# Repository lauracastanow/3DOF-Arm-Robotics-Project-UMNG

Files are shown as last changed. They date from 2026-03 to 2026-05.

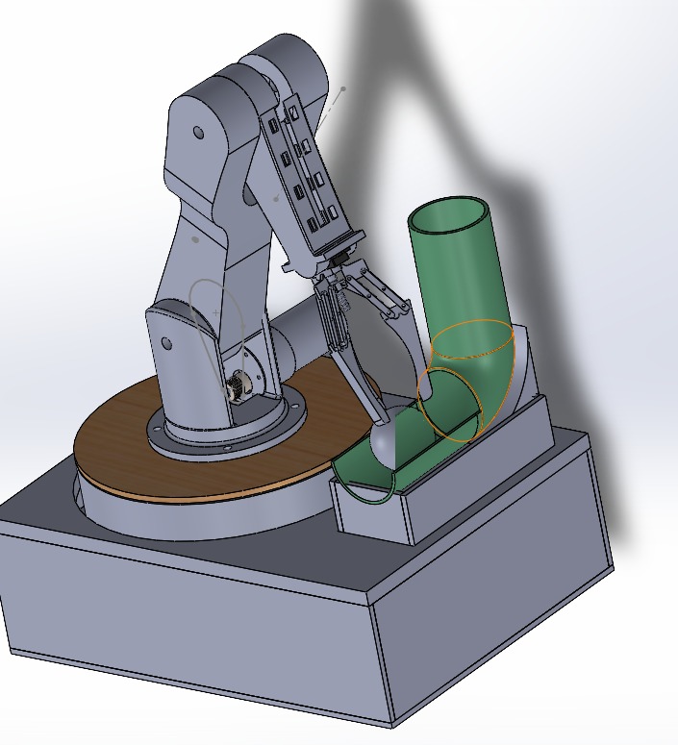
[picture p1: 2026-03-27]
Docs/Ensamblaje General SW.jpeg

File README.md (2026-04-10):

# 3DOF-Arm-Robotics-Project-UMNG
Este proyecto consiste en el diseño, modelado y simulación de un brazo robótico de 3 grados de libertad. En el siguiente repositorio, se incluye el desarrollo mecánico en CAD, simulación en software, código de control y una interfaz interactiva para visualizar la cinemática inversa. 

## Objetivos
### Objetivo General
Diseñar un brazo robótico integrando herramientas de hardware (CAD) y software (ROS 2, Gazebo, Python) para la posición del efector final mediante el cálculo de la cinemática y control de los actuadores en tiempo real.

### Objetivos Específicos
* Diseñar la estructura mecánica del brazo y su exportación a formato URDF.
* Modelar matemáticamente el sistema para implementar cinemática directa e inversa.
* Configurar con la simulación física en Gazebo Sim (Dynamics, colisiones e inercias).
* Establecer comunicación en tiempo real entre ROS 2 y Gazebo usando 'ros_gz_bridge'.
* Desarrollar una interfaz gráfica de usuario (GUI) interactiva para el control articular.

---

## Estructura del repositorio
El proyecto está modularizado basándose en el diagrama de bloques del sistema:

* 'Docs/' Diagramas de bloques, actas de trabajo y capturas de funcionamiento.
* 'Hardware/' Diseño CAD, mallas (meshes) y el archivo de descripción 'Ensamblee.urdf'.
* 'Simulación/' Archivos de lanzamiento ('gazebo.launch.py') y configuración del entorno virtual.
* 'Software/' Lógica de control, cinemática ('kinematics.py'), y nodo de ROS 2 conectado a la GUI ('gui.py')

---

## Descripción del sistema
El robot ("Bracito") es un manipulador que cuenta con los siguientes grados de libertad controlables:

* **Joint 1 (Base):** Rotación sobre el eje Z.
* **Joint 2 (Hombro):** Elevación del primer eslabón.
* **Joint 3 (Codo):** Elevación del segundo eslabón.
* **Joints 4, 5 y 6:** Pinza de 3 dedos configurada con plugins *Mimic* en Gazebo, permitiendo que la actuación de un solo motor cierre o abra la pinza completa de manera síncrona.

Ensamblaje General SolidWorks

El modelo permite calcular:
* Cinemática inversa
* Posición del efector final
Interfaz de Control Maestro y Gazebo funcionando

---

## Paquetes, Dependencias y Librerías
Para la correcta ejecución de etse proyecto, es necesario contal con el siguiente entorno:

**Entorno Base:**
* Ubuntu 24.04 (o compatible)
* [ROS 2 Jazzy] (https://docs.ros.org/en/jazzy/index.html)
*  Gazebo Sim (Harmonic)

**Librerías de Python:**
* 'rclpy' (Cliente de ROS 2 para Python)
* 'PyQt5' (Desarrollo e la interfaz gráfica)
* 'numpy' (Cálculos matriciales para la cinemática)

**Paquetes de ROS 2 utilizados:**
* 'robot_state_publisher': Para publicar el estado del robot basado en el URDF.
* 'ros_gz_sim': Para instanciar (spawn) el modelo en Gazebo.
* 'ros_gz_bridge': Para traducir los tópicos de 'JointState' / 'Float64' entre ROS 2 y Gazebo.

---

## Autoras
Proyecto desarrollado por estudiantes de Ingeniería de la Universidad Militar Nueva Granada (UMNG):
* **Laura Daniela Castaño Silva**
* **Carol Tatiana Jeréz González**

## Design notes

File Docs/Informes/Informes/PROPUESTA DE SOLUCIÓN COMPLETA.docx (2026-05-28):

## PROPUESTA DE SOLUCIÓN COMPLETA

Castaño Silva Laura Daniela, Carol Tatiana Jérez González, Hugo Alejandro Chacon Valderrama

{est.laura.castano, est.carol.jerez, hugo.chacon}@unimilitar.edu.co

Profesor: Alexandra Elizabeth Velasco Vivas

I. PROCEDIMIENTO

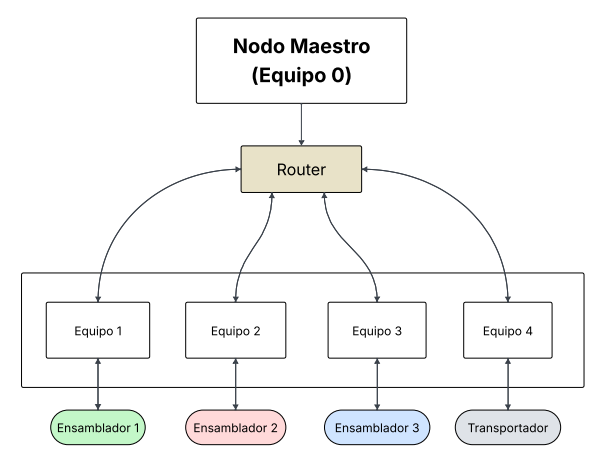
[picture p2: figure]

Figura 1. Diagrama de Bloques - Parte General.

En este caso, se va a mantener el mismo ideal de tener 5 equipos en funcionamiento, donde los equipos del 1 al 4 van a estar a cargo de los ensambladores y el transportador, sin embargo, el equipo 0 se va a usar para la comunicación general de todos los equipos, en este caso, se busca hacerlo por medio de un Router.

En este caso, seríamos el ensamblador tres.

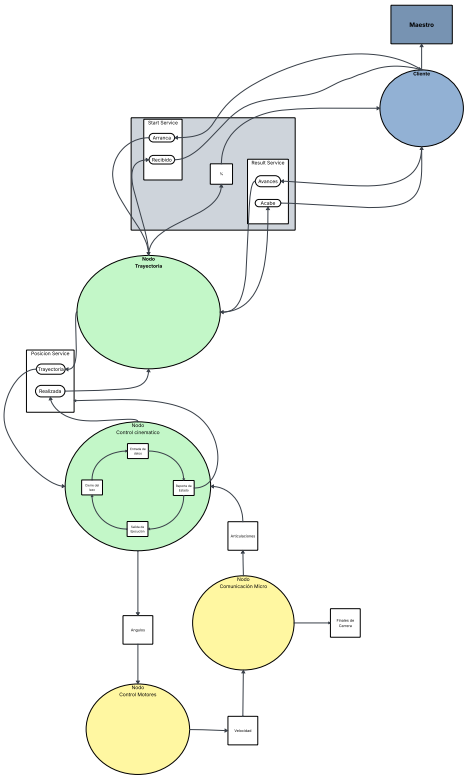
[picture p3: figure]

Figura 2. Diagrama de Bloques con cada nodo.

Para la implementación de la etapa de control se plantea un funcionamiento basado en el entorno de trabajo dispuesto por “Robot Operating System 2” - “ROS ²” el cual permite la comunicación coordinada entre los sistemas internos de un robot así como entre sistemas independientes (otros robots) por medio del intercambio de datos entre “nodos” dedicados por sistema (Control, Sensores, Actuadores, Cinemática Directa\Inversa, Robot 1, Robot 2,..etc) y sus respectivos códigos de funcionamiento.
Los “Nodos” están programados para interactuar a Través de una estructura de “Cliente” y “Publisher” que se comunican mediante un orden basado en “Tópicos” y “Suscripciones”.

Para este caso se propone un a serie de nodos de información sistema (ensamblador) enfocados en la comunicación de datos relacionados a las cinemáticas, trayectorias y Ángulos del prototipo, con el objetivo de ser procesados en un microcontrolador asociado con el fin de ser manipulado desde una estación de control “Maestro” por un usuario

Planos

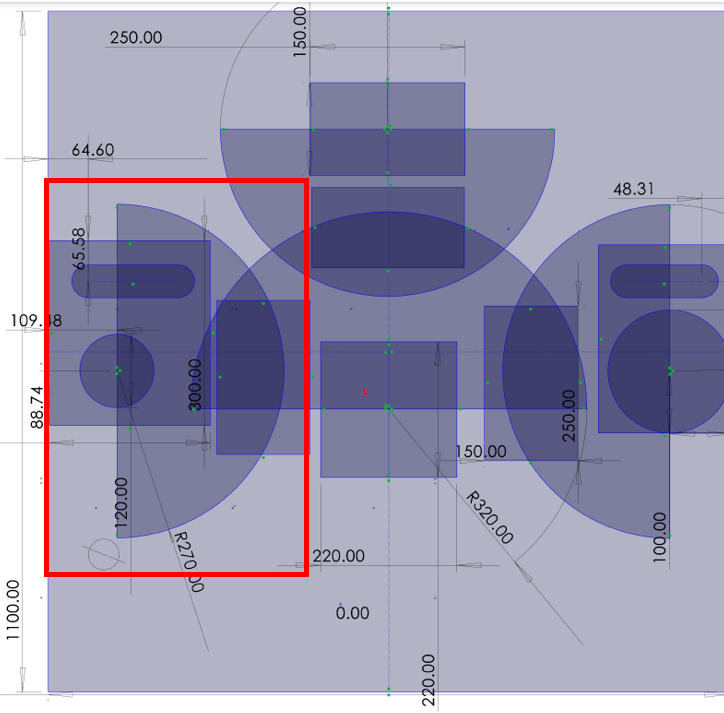
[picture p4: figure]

Figura 3. Plano Espacio de trabajo de sistema integrado.

El robot ensamblador se ubicara al lado izquierdo el espacio de trabajo del sistema complejo, este se encontrara frente al robot transportador el cual le entregara el cuerpo al cual ubicar los elementos deseados, así mismo los demás ensambladores están alrededor del transportador para esperar el cuerpo a ensamblar una vez este haya terminado de ensamblar los elementos.

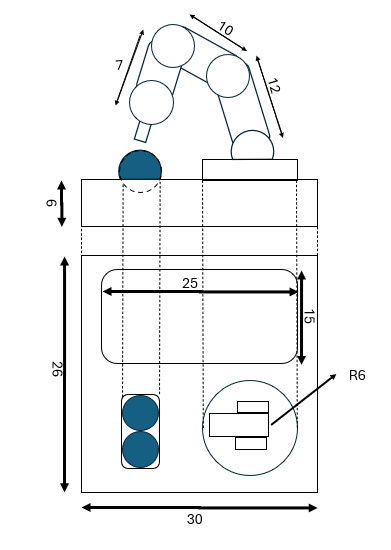
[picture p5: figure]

Figura 4.Boceto robot ensamblador.

El robot ensamblador es un robot antropomórfico el cual cuenta con tres grados de libertad y un radio de trabajo de 29 cm, con un base de 30x26 cm donde se tiene el espacio para posicionamiento de pinpones de un tamaño de 25x15 cm y sistema de almacenamiento por los elementos a ubicar.

Así mismo el brazo se realizará con impresión 3D para elementos de soportes, articulaciones bases y MDF para elementos necesariamente livianos como eslabones. Los movimientos de articulaciones se realizan con motores con encoder, el gripper utilizará un servomotor.

RVIZ

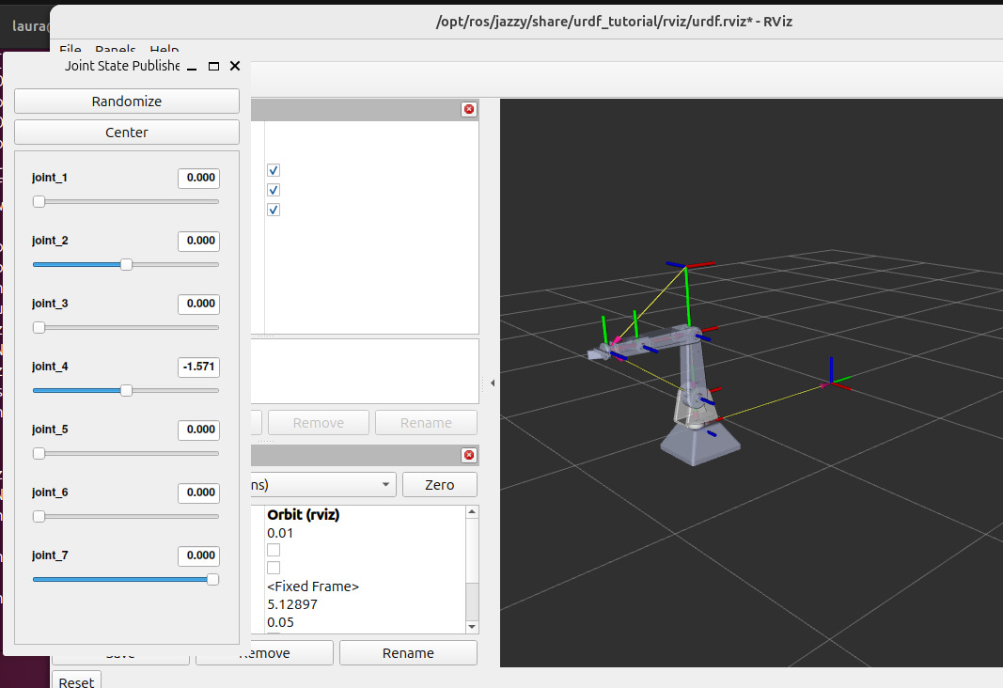
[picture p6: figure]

Figura 5. Brazo en RViz.

A pesar de que se encuentre un robot con 4 grados de libertad, se ha tomado la decisión de disminuirlo a 3 grados de libertad, ya que se le quitará un grado de libertad de la parte final del brazo para no hacer tan complejo el diseño y evitar más peso que complique el ensamblaje al momento de empezar a ensamblar.

Por otro lado, los materiales que vamos a emplear son:

- Base del motor: Impresión 3D, donde buscaremos dejar un hueco para poner toda la parte eléctrica dentro.
- Caja cilíndrica: impresión 3D y la parte de la tapa en MDF.
- Balineras: Usaremos un mecanismo de balineras para la caja cilíndrica para la parte rotatoria.
- Articulaciones: En MDF y para que no sean tan pesadas, se harán en láminas sin llegar a dejar el brazo muy grueso.
- 3 motores encoder y un servomotor que se implementará para el gripper evitando problemas de peso.
- Gripper: impresión 3D y en las puntas se buscará poner una goma o esponja suave para que le sea más fácil agarrar los pimpones.

El presente documento corresponde a un informe de práctica de laboratorio de “Robótica” presentado en la Universidad Militar Nueva Granada durante el periodo 2025-1.

INFORME DE PRÁCTICA DE LABORATORIO Versión 1.0 PROGRAMA DE INGENIERÍA MECATRÓNICA Periodo 2025-1

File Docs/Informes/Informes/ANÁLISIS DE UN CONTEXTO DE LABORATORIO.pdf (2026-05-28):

INFORME DE PRÁCTICA DE LABORATORIO | Versión 1.0
PROGRAMA DE INGENIERÍA MECATRÓNICA
Periodo 2026-1

# ANÁLISIS DE UN CONTEXTO DE LABORATORIO

Castaño Silva Laura Daniela, Carol Tatiana Jérez González {est.laura.castano, est.carol.jerez}@unimilitar.edu.co

Profesor: Alexandra Elizabeth Velasco Vivas Resumen— El proyecto consiste en el diseño e implementación de un robot manipulador antropomórfico de 3 GDL integrado en un espacio de trabajo de ensamblaje manual.

El robot tiene la tarea de asistir al ensamblaje por medio del usuario mediante la ejecución de tareas de pic-and-place de tres pimpones desde una zona de recogida hacia una bandeja de depósito con posiciones predefinidas.

El entorno es una celda de trabajo controlada de 300 x 220 mm, donde los pimpones están organizados de manera vertical con una separación de 16 mm entre sí. Esta configuración permite que el robot opere sin necesidad de visión artificial, basándose en la precisión de la cinemática y planeación de las trayectorias.

Abstract—- The project involves the design
and | implementation | of | a | 3-axis
anthropomorphic | manipulator | robot
integrated | into | a | manual | assembly
workspace.

The robot is tasked with assisting the user
during | assembly | by | performing
pick-and-place tasks involving three pins, moving them from a pickup area to a drop tray with predefined positions.

The environment is a controlled 300 x 220 mm work cell, where the pins are arranged vertically with a 16 mm spacing between them. This configuration allows the robot to operate without the need for machine vision, relying instead on the precision of its kinematics and trajectory planning.

Palabras clave -. trayectoria trapezoidal,
cinemática | inversa, | controladores,
posiciones, Gazebo, DH.
I. INTRODUCCIÓN

Se abordó la tarea de pick & place, el cual consiste en recoger un objeto, en este caso, el pin pon en una posición conocida y depositarlo en una bandeja la cual se encuentra ubicado también en una posición conocida.

Por lo que, cada tarea la debe hacer tres veces, debido a que son 3 pimpones, debe recoger cada uno y depositarlo en la bandeja.

Debido a que los objetos a manipular poseen dimensiones constantes y posiciones de recogida y depósito conocidas, el diseño se centra en:

- La configuración cinemática: un brazo RRR que permite alcanzar los puntos de la bandeja y la zona de recogida dentro del plano de trabajo.
- Planeación | de | trayectorias:
implementación | de | perfiles | de
velocidad trapezoidales para garantizar movimientos suaves con una velocidad máxima de 1.8 rad/s.
- Control cinemático: uso de parámetros por medio de Denavit-Hartenberg (DH)
y | cinemática | inversa | para | el
posicionamiento preciso del efector final.

El presente documento corresponde a un informe de práctica de laboratorio de “Robótica” presentado en la Universidad Militar Nueva Granada durante el periodo 2026-1.

Se tiene en cuenta el siguiente diagrama con las cotas:

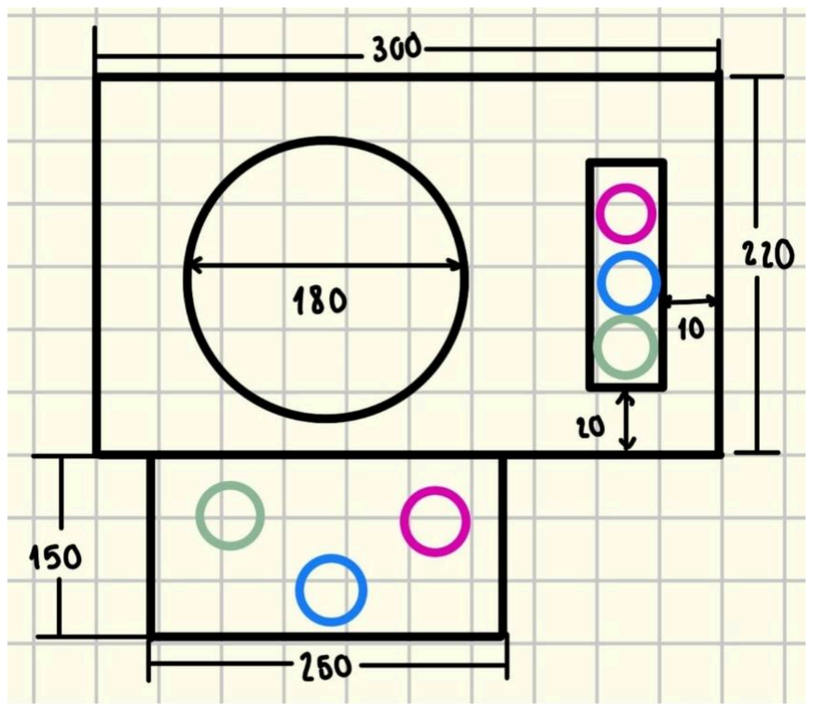
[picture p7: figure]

Figura 1. Espacio de la base del robot

a = [195, 180, 125] mm — longitudes de eslabón

d = [0, 0, 0] mm — desplazamientos axiales

α = [90°, 0°, 0°] — ángulos de torsión

Rango articular: q1 ∈ [-180°, 180°], q2 ∈ [-120°, 120°], q3 ∈ [-150°, 150°]

II. ESPACIO DE TRABAJO

Del plano simulado del ensamblaje físico de la celda de trabajo se lograron identificar los siguientes elementos para el planteamiento de los puntos de la trayectoria:

1. Zona de recogida (rectángulo pequeño, 40 × 48 mm, ubicado a la derecha del área principal): Contiene tres pelotas de ping pong apiladas verticalmente, separadas 16 mm entre sí.
2. Bandeja de depósito (rectángulo superior, 250 × 150 mm): Contiene tres slots donde se depositan las pelotas. Su centro está ubicado aproximadamente a 200 mm del origen en el eje Y.
3. Origen del sistema de coordenadas: Centro de la base giratoria del brazo (centro del círculo D =180 mm en el plano).

Las coordenadas cartesianas de cada punto, expresadas en mm respecto al origen, son:

Punto | Tipo | X(mm) | Y(mm) | Z(mm)
p1 | Recogida pingpong 1 | 129.93 | -22.91 | 228.11
p2 | Recogida ping pong 2 | 129.93 | -22.91 | 228.11
p3 | Recogida ping pong 3 | 129.93 | -22.91 | 228.11
P1 | Depósito bandeja slot 1 | -43.45 | -115.5 1 | 192.74
P2 | Depósito bandeja slot 2 | 0 | -189.2 | 170.85
P3 | Depósito bandeja slot 3 | 35.92 | -155.6 1 | 190.39
reposo | Posición inicial/final | 125.0 | 0 | 375.0

Para ello, se definieron dos alturas de operación:

- Z = 110 mm para recogida y depósito
- Z = 180 mm como altura de tránsito entre puntos

Esto con el propósito de evitar colisiones durante los desplazamientos.

Requisitos Funcionales y Restricciones Técnicas
Requisitos Funcionales (RF):
- RF1: Recoger tres pimpones de forma secuencial desde una pila vertical en la zona de recogida.

- RF2: Depositar cada pimpón en un slot específico de la bandeja de depósito (250 x 150 mm)
- RF3: Ejecutar trayectorias que incluyan una altura de tránsito segura (Z = 180 mm) para evitar colisiones entre los puntos de operación (Z = 110 mm).
- RF4: mantener comunicación constante entre la interfaz de usuario y el simulador (Gazebo/Ros2) para la verificación de estados.
Restricciones | Técnicas | (Requisitos | No
Funcionales)
- RNF1: La velocidad articular debe limitarse a un rango de 0 a 2 rad/s para proteger los actuadores y garantizar seguridad.
- RNF2: El rango articular de los eslabones debe respetarse: q1 ∈ [-180°, 180°], q2 ∈ [-120°, 120°], q3 ∈ [-150°, 150°]
- RNF3: El sistema debe operar bajo control PID para asegurar que las posiciones reales sigan las trayectorias calculadas.
- Consumo Energético: Cuando los PID están mal sintonizados, los motores empiezan a vibrar, en este caso, no sucede esto, tal cual se puede observar en la Figura 2.

Relación de Necesidades del Contexto y Criterios de Diseño
- Interacción Humano-Robot: Dado que el usuario actúa como ensamblador en el mismo espacio, el diseño del robot
prioriza | trayectorias | suaves | y
predecibles para facilitar la supervisión humana y minimizar riesgos.
- Eficiencia de Espacio: El robot se sitúa en un origen central de 180 mm respecto al diámetro de la base, para maximizar su área de cobertura dentro de los límites de la celda de ensamblaje.
- Aspecto Social y Educativo: En un entorno de laboratorio, el sistema sirve como herramienta de aprendizaje para la validación de modelos matemáticos (cinemática inversa) y su aplicación en procesos industriales de automatización de bajo costo.
- Aspecto Económico: El uso de una configuración antropomorfa de 3 GDL con control de velocidad simplificado permite una implementación económica utilizando componentes accesibles, ideal para celdas de ensamblaje pequeñas o prototipos educativos.

Profundización en Telemetría e Interfaz (Indicador 2.1)
- Análisis de Error donde se denota el seguimiento de Trayectoria, donde se puede observar la diferencia entre la posición deseada (generada por CSV) y la posición real que reporta Gazebo. Justificando el control del PID.

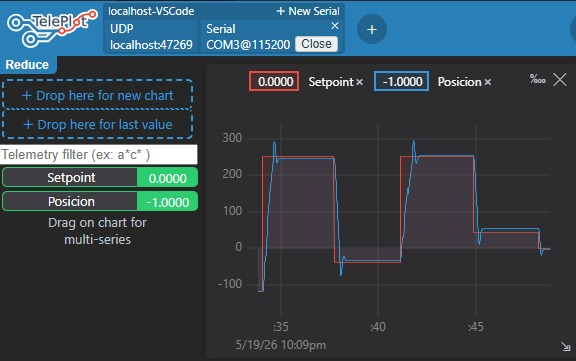
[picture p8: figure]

Figura 2. Diferencia de error de la posición del motor 1 en implementación.

- Validación de la Cinemática Inversa: donde se permite confirma que para una coordenada X, Y,Z dada, el robot calcula y alcanza los ángulos, para ello, en la parte de la implementación se ponen acelerómetros y un sensor hall con la finalidad de que el motor no se pierda en cada una de las trayectorias dadas. Por ejemplo, en la posición de
"Home", | el | sistema | reporta
exactamente (125, 0, 375) mm, lo que confirma que el modelo matemático coincide con el simulado.
- Monitoreo de Errores: La diferencia entre el ángulo deseado y el ángulo real se observa en Gazebo (Q1: -10°, Q2: 32°, Q3: 41° al recoger el primer pimpon). Esto justifica la necesidad de los controladores PID para minimizar el error de estado estacionario.

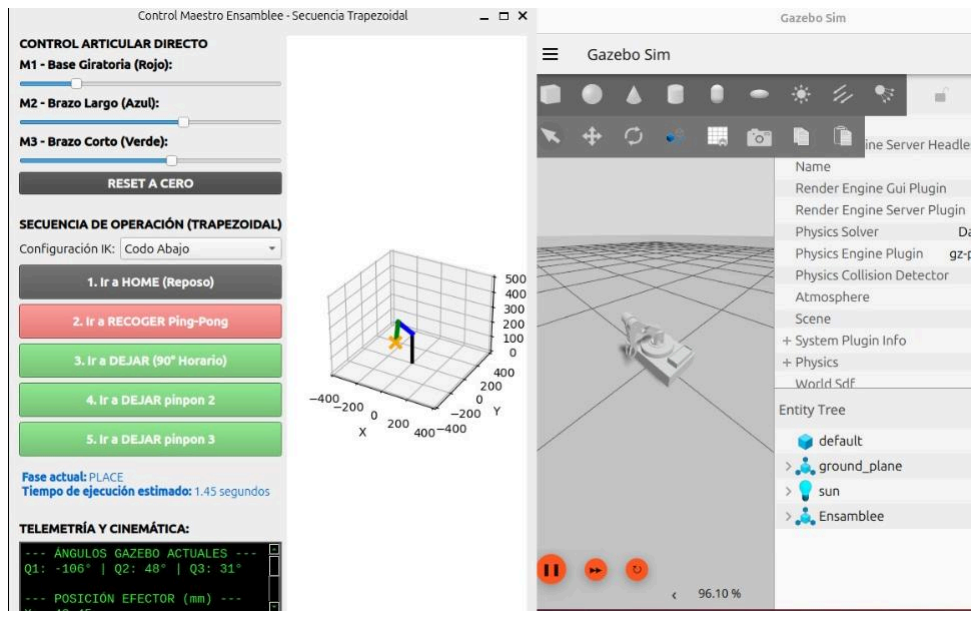
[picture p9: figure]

Figura 3. Verificación en Gazebo.

Profundización en Simulación con Gazebo Gazebo se determina como el motor físico donde:
- Detección de Colisiones: en el entorno de Gazebo se definen los límites del robot para hacerlo más realista respecto a cómo se debería de comportar el robot en la parte de implementación, debido a eso, se limitan los ángulos a los que puede llegar cada uno de los eslabones.
- Modelado de la Carga: El diseño del efector final, se compone de dos dedos los cuales tienen en cuenta el diámetro de 4 mm del pimpon, para ello, aunque el peso sea mínimo, se tiene en cuenta al igual que la altura para evitar colisiones al momento en el que el eslabón superior baje sea para recoger o dejar pimpon.
- Singularidades: Debido a que es un robot antropomórfico tiene puntos donde se pierde grados de libertad cuando el brazo se encuentre totalmente extendido. Para ello, Gazebo me ayudó a identificar las trayectorias que se encuentran lejos de las singularidades.

Parámetros de Diseño y Contexto (Indicar 1.3)

- Seguridad Colaborativa: se limitó la velocidad articular a 1.8 rad/s, esto con la finalidad de poder tener mayor reacción al momento de que se tenga algún problema sea en tema de trayectorias o evitar que algunos de las piezas del robot lleguen a colapsar o se dañen como podría suceder a altas velocidades.
- Repetibilidad vs. Exactitud: Para poder colocar cada uno de los pimpones en huecos de 20 mm se necesita alta repetibilidad validado mediante las gráficas de posición vs. tiempo.
- Espacio de Trabajo: Opera en un área de 300 x 220 mm con una base de 180 mm de diámetro.
- Optimización del Workspace: La configuración antropomórfica (RRR) fue elegida sobre una SCARA porque permite alcanzar las pelotas apiladas verticalmente (separación de 16 mm)
con | mayor | facilidad | al | tener
articulaciones de hombro y codo rotacionales.
- Zonas de Seguridad: Z=110 mm para operación y Z=180 mm para tránsito. Esta franja de seguridad de 70 mm es el criterio de diseño para evitar colisiones con otros elementos de la celda de ensamblaje mientras el robot se desplaza entre la zona de recogida y la bandeja.

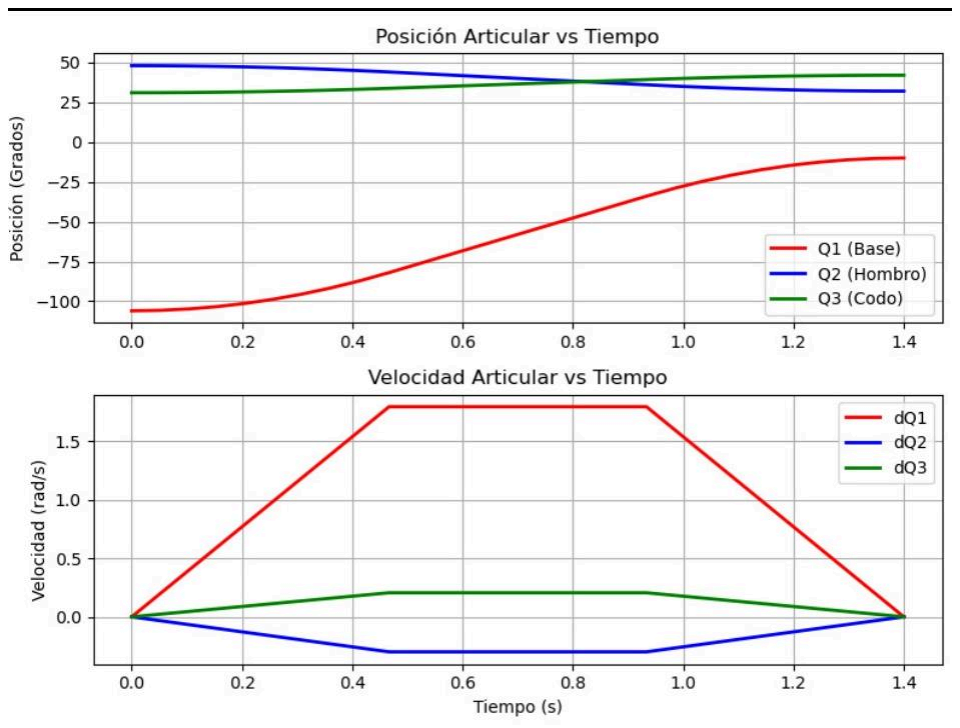
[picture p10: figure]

Figura 4. Gráfica y aceleraciones de recoger pinpon.

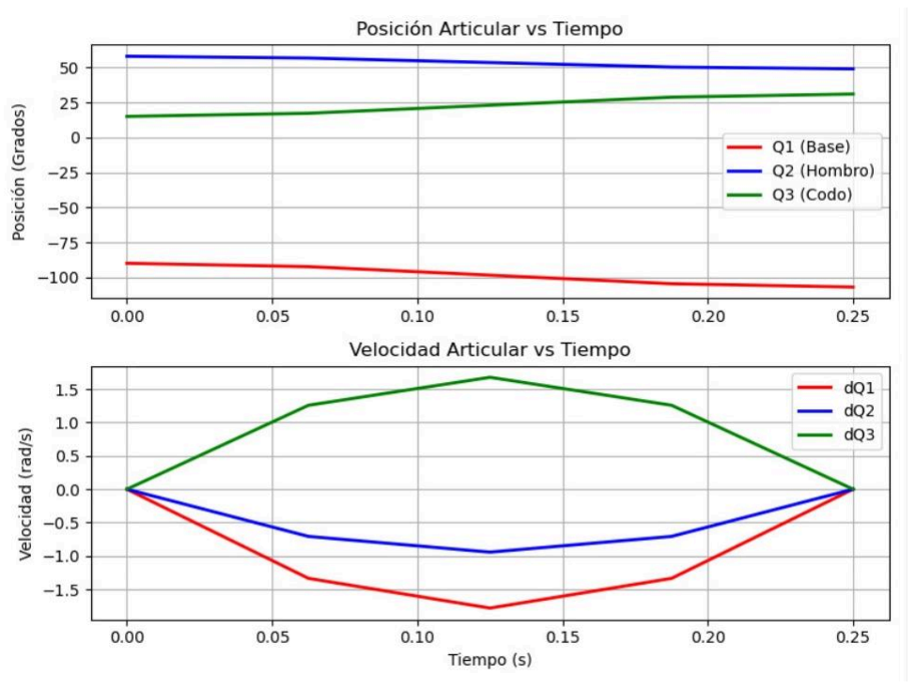
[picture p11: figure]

Figura 5. Gráfica y aceleraciones para dejar primer pin pon.

También, se tienen en cuenta los siguientes datos:
- Configuración: RRR con longitudes de eslabón a=[195, 180, 125] mm.
- Límites | Articulares: | q1(± 180°),
q2(± 120°), q3(± 150°).
- Puntos de Operación Críticos: Desde Home hasta los slots de la bandeja (P1, P2, P3) con coordenadas X, Y, Z específicas validadas por telemetría.

Discusión de Resultados
En la fase de simulación en Gazebo, se validó
que | el | modelo | cinemático | inverso
implementado responde con precisión a los puntos de consigna definidos en el archivo CSV. Al analizar la telemetría obtenida:
- Precisión Posicional: Se observó que el error entre la posición deseada y la
posición | real | del | efector final
(coordenadas X, Y, Z de la matriz T_{03}) es despreciable, lo que confirma una correcta sintonización de los controladores PID.
- Comportamiento | Dinámico: | Las
gráficas de Velocidad Articular vs. Tiempo muestran un perfil trapezoidal suave. Al limitar la velocidad a 1.8 rad/s (90% de la capacidad máxima de los actuadores), se eliminaron los picos de aceleración que podrían causar
inestabilidad | al | manipular | los
pimpones.
- Sincronización de Interfaz: La
interfaz | de | telemetría | permitió
identificar en tiempo real el estado de las articulaciones (Q1, Q2, Q3), facilitando la detección de posibles colisiones antes de ejecutar el movimiento en el plano de trabajo real.

Conclusiones
Cumplimiento de Requisitos: Se logró el diseño de un sistema de trayectorias capaz de realizar el ciclo completo de pick-and-place para tres elementos, respetando las restricciones de altura de tránsito (Z=180 mm) y operación (Z=110 mm).
Eficacia de la Configuración: La arquitectura antropomórfica de 3 GDL resultó ser la más adecuada para el contexto de laboratorio, permitiendo una gran maniobrabilidad en un espacio reducido (300 x 220 mm) sin sacrificar la precisión necesaria para la disposición en la bandeja.
Validación Digital: El uso de herramientas de simulación (Gazebo/ROS2) y la exportación de datos mediante CSV permitieron una transición segura hacia el hardware, garantizando que los límites articulares (180°, 120°, 150°) no fueran excedidos.

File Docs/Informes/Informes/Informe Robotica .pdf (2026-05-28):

# ROBOTS MANIPULADORES

Castaño Silva Laura Daniela, Carol Tatiana Jérez González {est.laura.castano, est.carol.jerez}@unimilitar.edu.co

Profesor: Alexandra Elizabeth Velasco Vivas

I. INTRODUCCIÓN

En el presente laboratorio se plantea la solución de un sistema automatizado de ensamble compuesto por robots manipuladores fijos, un transportador y tres estaciones ensambladoras. Se diseña uno de los robots
ensambladores, | específicamente | un
manipulador tipo antropomorfo de tres grados de libertad (3 GDL), seleccionado por su eficiencia y precisión en tareas de ensamblaje.

El sistema será modelado y simulado, integrando una interfaz de control vinculada a ROS2, lo que permitirá supervisar y operar el robot dentro del entorno de simulación.
Además, | se | presentan | los | bocetos
correspondientes a la parte mecánica y eléctrica del robot, con el fin de evidenciar su diseño estructural y la integración de los componentes de control y potencia.

II. DESARROLLO
Diagrama de Bloques

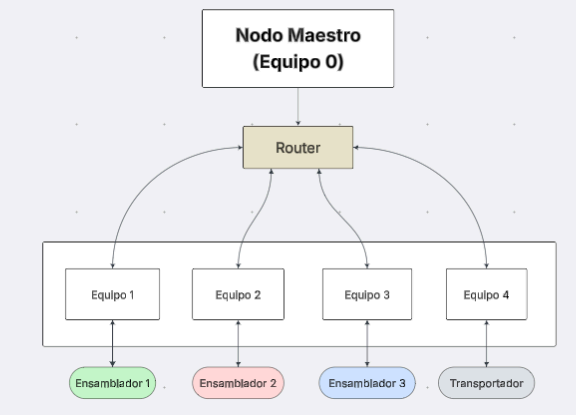
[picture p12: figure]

Figura 1. Diagrama de bloques general

Se va a mantener el ideal de tener 5 equipos en funcionamiento, donde los equipos del 1 al 4 van a estar a cargo de los ensambladores y el transportador, sin embargo, el equipo 0 se va a usar para la comunicación general de todos los equipos, en este caso, se busca hacerlo por medio de un Router.
En este caso, seríamos el ensamblador tres.

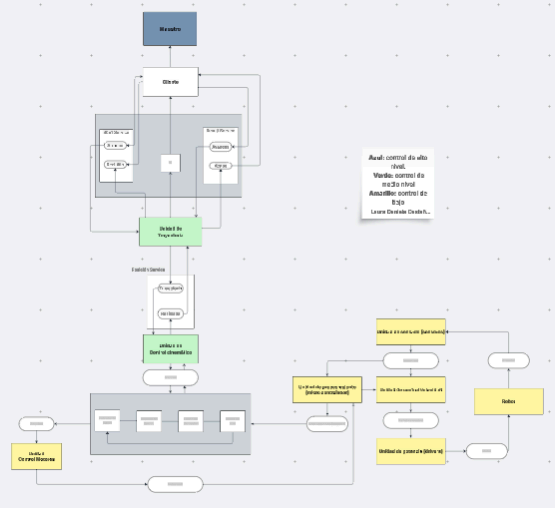
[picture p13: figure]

Figura 2. Diagrama de Bloques con cada nodo.

Para la implementación de la etapa de control se plantea un funcionamiento basado en el entorno de trabajo dispuesto por “Robot Operating System 2” - “ROS ²” el cual permite la comunicación coordinada entre los sistemas internos de un robot así como entre sistemas independientes (otros robots) por medio del intercambio de datos entre “nodos” dedicados por sistema (Control, Sensores, Actuadores, Cinemática Directa\Inversa, Robot 1, Robot 2,..etc) y sus respectivos códigos de

funcionamiento.
Los “Nodos” están programados para interactuar a Través de una estructura de “Cliente” y “Publisher” que se comunican mediante un orden basado en “Tópicos” y “Suscripciones”.

Para este caso se propone un a serie de nodos
de | información | sistema | (ensamblador)
enfocados en la comunicación de datos relacionados a las cinemáticas, trayectorias y Ángulos del prototipo, con el objetivo de ser procesados en un microcontrolador asociado con el fin de ser manipulado desde una estación de control “Maestro” por un usuario.

Diseño.

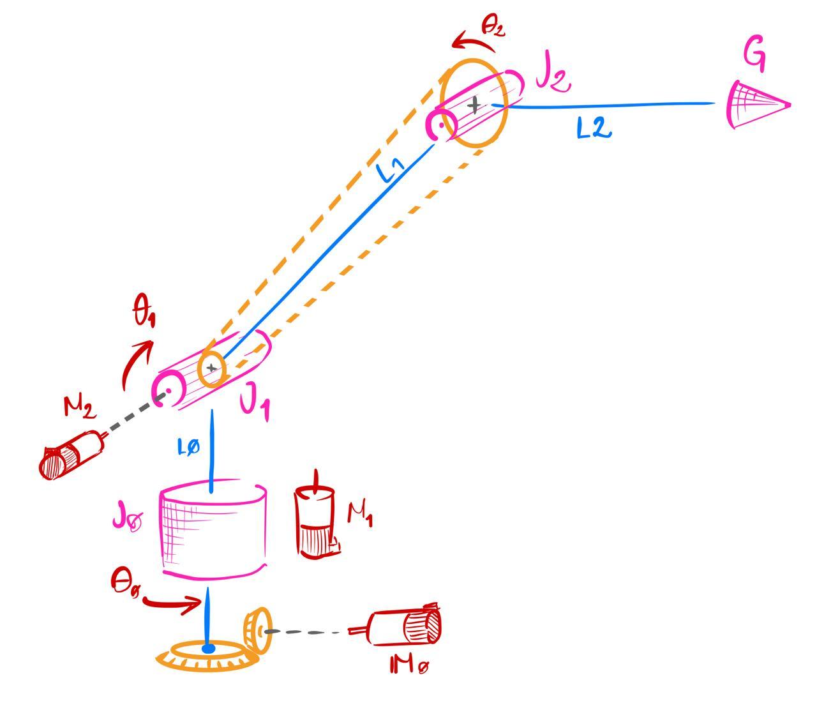
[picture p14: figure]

Figura 3. Esquema básico del manipulador.

El manipulador a realizar consta de dos sistemas de correa para junturas rotacionales principales permitiendo una fácil transmisión de movimiento en los eslabones, un sistema rotatorio vertical en su base conformado por dos piñones cónicos, permitiendo una velocidad suave y un torque eficiente teniendo en cuenta el peso resultante del brazo, el sistema de agarre se compone de un gripper sub actuado de tres dedos adaptado a la forma y tamaño de los elementos a ensamblar mejorando su estabilidad sin exceso de actuadores.

Diseño power point

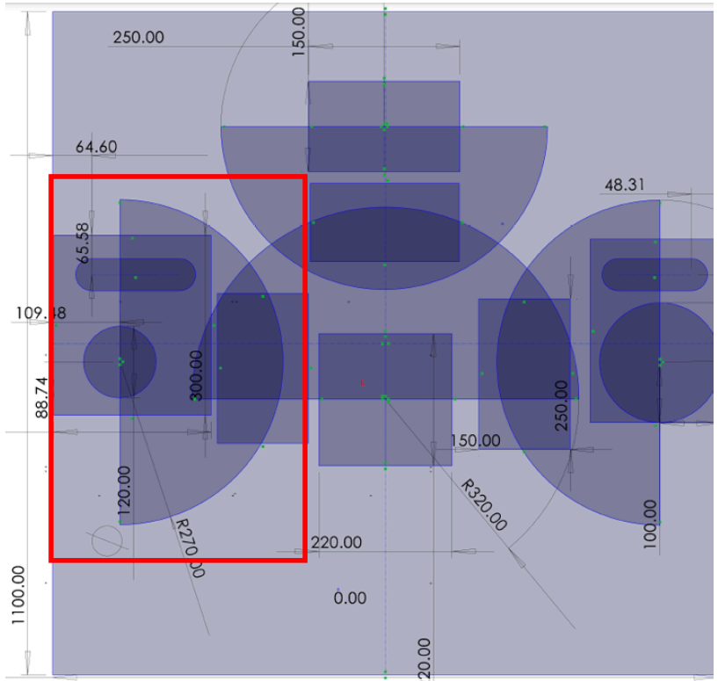
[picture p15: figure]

Figura 4. Plano de espacios. Para el diseño grupal se tuvieron en cuenta unas coordenadas locales que eran respecto al ensamblador de cada equipo y unas coordenadas globales respecto al centro del transportador.

Coordenadas Locales con las dimensiones del plano Final

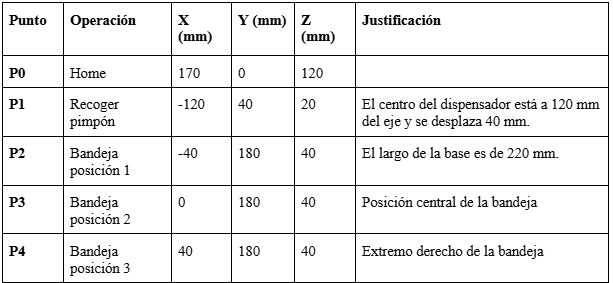
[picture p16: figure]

Cálculo de las variables de juntura

### 1. Cálculo de la Rotación de la Base θ

1
Articulación que orienta el brazo hacia el objetivo en el plano XY.
θ

1 = atan2(y, x)
Para recoger se tiene: P1 (-120, 40)
→ θ

1 = atan2(40, − 120) = 161. 56° Para dejar: P2 (0, 180)
→ θ

1 = atan2(180, 0) = 90°

### 2. Cálculo de Hombro θ

2
Para el punto de recogida P1

→ r = (− 120)

2
+ (40)

2 = 126. 5 mm

z

rel = 20 − 75 =− 55 mm
Depende del ángulo de inclinación hacia el punto y el ángulo interno del triángulo formado por los eslabones.

### 3. Cálculo de Codo θ

3
cos(θ
3

) =

r

2
+z
rel

2 −L
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
Coordenadas Globales

Planos mecánicos

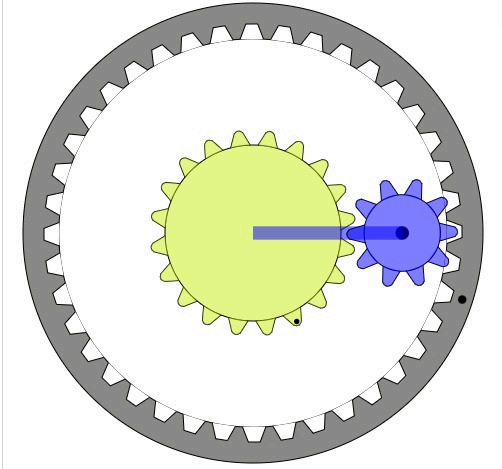
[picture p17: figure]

Figura 5. Planetario para la base rotatoria.

El sistema mostrado en la imagen es un reductor de velocidad planetario. Este componente permite convertir la alta velocidad y bajo torque de un motor DC en el alto torque y baja velocidad necesarios para mover las articulaciones del manipulador. Pues se compone de lo siguiente:
- Engranaje Sol (Amarillo): Es el engranaje central que recibe el giro directo del eje del motor.
- Planetas (Morado): Engranajes que rotan sobre sus propios ejes mientras orbitan alrededor del sol.
- Portaplanetas (Brazo amarillo): Estructura que une los centros de los planetas y transmite el movimiento final al siguiente eslabón del robot.
- Anillo o Corona (Gris exterior): Engranaje interno fijo que obliga a los planetas a desplazarse circularmente.

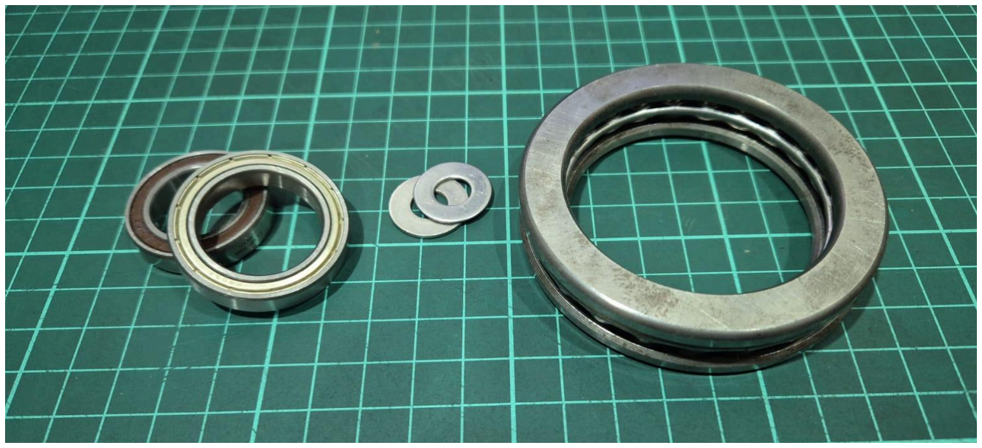
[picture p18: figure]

Figura 6. Rodamientos.

Con el fin de reducir las perturbaciones en el sistema y garantizar un funcionamiento continuo de los elementos dinámicos se hará uso de los rodamientos industriales tanto radiales en los eslabones como axiales en la base.

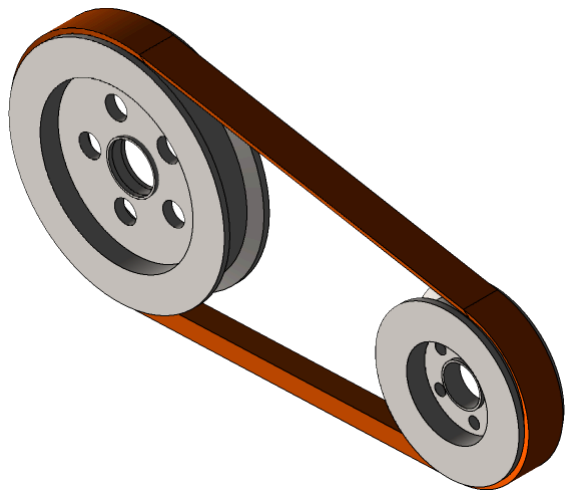
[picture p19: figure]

Figura 7. Sistema de transmisión con correas.

Para el movimiento de los eslabones se optó por un sistema polea con el fin de ubicar los actuadores en puntos estratégicos y así reducir peso en las articulaciones y espacio en ellas, del mismo modo ayuda con movimiento suaves y controlados.Por ultimo este sistema nos facilita el reemplazo y mantenimiento en caso de cambio o daños.

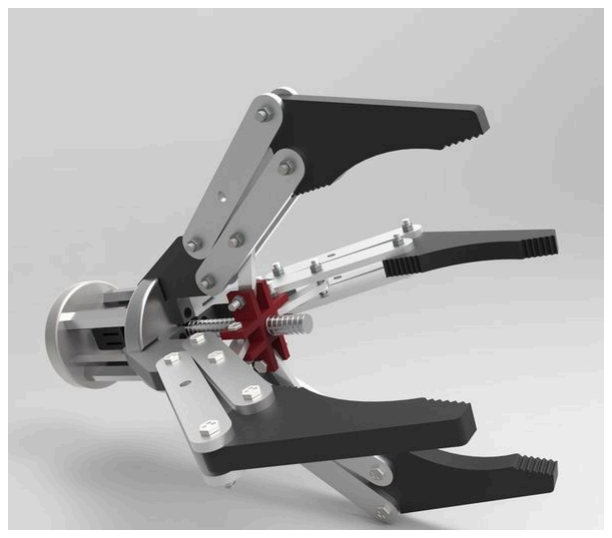
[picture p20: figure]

Figura 8. Sistema de agarre de los pinpones.

El sistema de agarre está compuesto por una pinza de tres asociada por medio de un tornillo sin fin el cual permite el control de movimiento. Estas pinzas están diseñadas para adaptarse a la geometría de los pinpones y una capa de material esponjado para aumentar la fricción.

Planos electricos
En la parte eléctrica se tiene pensado el uso de motores de corriente directa con drivers TB6612FNG el cual soporta corrientes de hasta 1A y permite el control de dos motores por módulo. Para el sensor de variables como posición y velocidad se utilizan encoders en los respectivos motores.

Convención

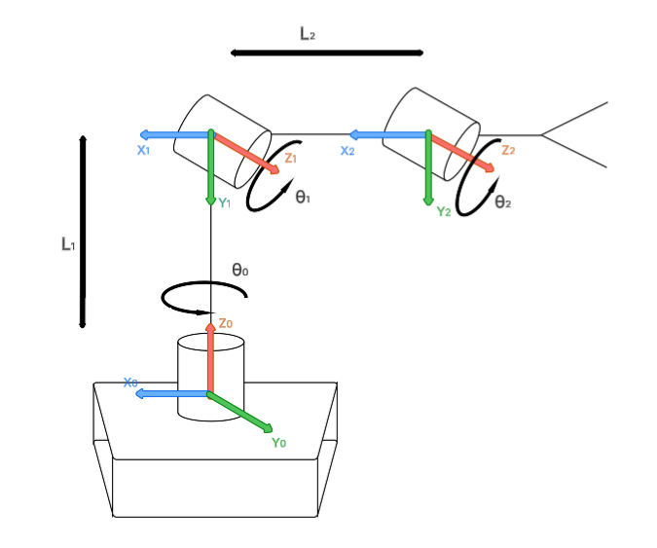
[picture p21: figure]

Figura 8. Convención del sistema.

Presentamos una asignación de marco de referencia, para el manipulador tiene como eje de referencia rotatorio el eje Z y con respecto a
este | se | realiza | la | convención | de
Denavit–Hartenberg (DH).
Links | θi | di (mm) | ai (mm) | αi
1 | θ1 | 75 | 0 | 90°
2 | θ2 | 0 | L1 = 250 | 0
3 | θ3 | 0 | L2 = 210 | 0

Ecuaciones de Torque en los ejes J1 y J2

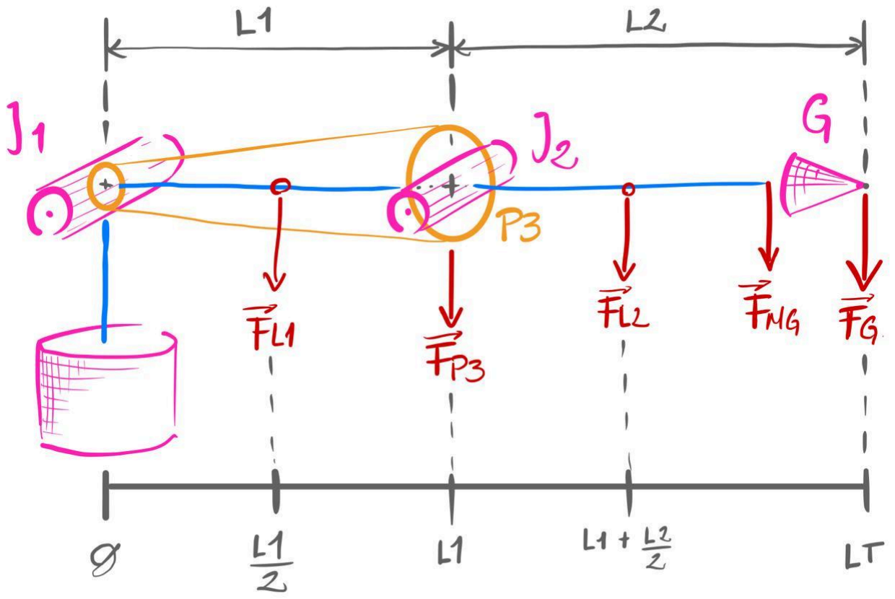
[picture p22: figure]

Figura 9. Diagrama cuerpo libre de torques.

Masas:
- Gripper Cargado (mG
)
- Motor Gripper (m
MG

)
- Polea 3 (m
P3

)
- Eslabón 1 (m
L1

)
- Eslabón 2 (m
L2

)
Distancias:
- Eslabón 1 (L1)
- Eslabón 2 (L2)
- LT = L1 + L2
- Gravedad (g)
Eslabón 1:Torque Máximo del sistema ΣT

J1 =

= g [ LT (mG + mMG

) + (L1 +

L2
2

)(mL2

) + (mP3 +

mL1
2

) ]

Eslabón 2:

ΣT

J2 = L2 * g [ mG + m

MG +

mL2

2

]

Matriz de Transformación
La matriz general de DH para cada eslabón:

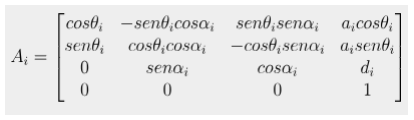
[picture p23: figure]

Sustituyendo los valores que ya se tienen d

1 = 75 mm, a

2 = 250 mm, a

3 = 210 mm, α

1 =

Matriz 1 de la cintura

Matriz 2 del hombro

Matriz 3 del codo

Se multiplican las matrices para obtener la Transformación Total usando la siguiente fórmula:

T
0

3 = A
1
- A
2
- A
3

Primera multiplicación de la cual obtenemos:

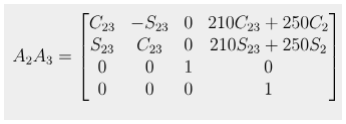
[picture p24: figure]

Esta matriz representa el brazo y el antebrazo moviéndose en un mismo plano.

La multiplicación final queda:

De la última columna de la matriz total, se extraen las ecuaciones que piden para calcular la posición (x,y,z) del efector final:
1. P
x = cos θ
1

( ) 210cos θ
2 + θ
3
( | ) + 250cos(θ
| 2
[ | )]
2. P
y = sen θ
1

( ) 210cos θ
2 + θ
3
( | ) + 250cos(θ
| 2
[ | )]
3. P
z = 210sen θ

2 + θ
3
( | ) + 250sen(θ
2

) + 75

Validación de las posiciones con MatLab Para validar el comportamiento del robot diseñado, se implementó un script en MATLAB que calcula la posición del efector final (X,Y,Z) a partir de las ecuaciones obtenidas de la matriz de transformación homogénea. Se dividió en dos fases:
1. Validación por Inspección Geométrica: En esta sección, el código define las dimensiones de los eslabones y evalúa tres posturas conocidas para asegurar que las ecuaciones sean correctas (vertical Total, brazo en L y extensión total).
2. Implementación de las Ecuaciones de Cinemática Directa: El script utiliza
las | funciones | trigonométricas
derivadas | del | modelo | de
Denavit-Hartenberg para transformar los ángulos de las articulaciones q en coordenadas cartesianas
1,

q
2,

q
3
P

x = cos θ
1

( ) 210cos θ
2 + θ
3
( | ) + 250cos(θ
| 2
[ | )]

P

y = sen θ
1

( ) 210cos θ
2 + θ
3
( | ) + 250cos(θ
| 2
[ | )]

P

z = 210sen θ

2 + θ
3
( | ) + 250sen(θ
| 2

) + 75

Estas fórmulas permiten que el software calcule la posición exacta del efector final antes de enviar los comandos al simulador ROS2/RViz.

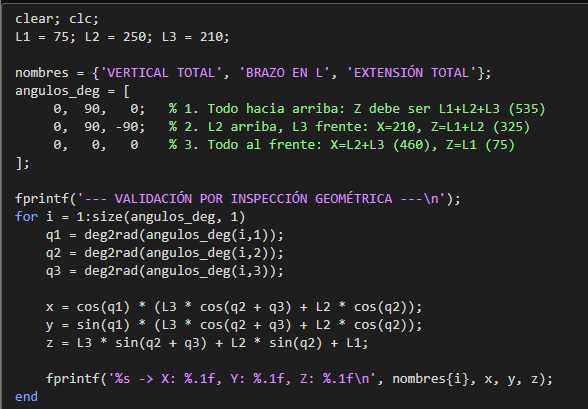
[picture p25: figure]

Figura 10. Relación de coordenadas cartesianas.
3. Aplicación a las Tareas del Proyecto Final: Finalmente, el código aplica estas ecuaciones a los puntos específicos de la operación de
ensamble | definida | (HOME,
RECOGER EN PI Y DEJAR EN P3)


Figura 11. Aplicación a las Tareas del Proyecto Final
Donde obtuvimos lo siguiente:

Figura 12. Posición alcanzada con la validación por Matlab.

Lo cual demuestra que es necesaria la cinemática inversa para este tipo de casos, ya que si no, solo se puede tantear con ángulos para llegar a una posición cercana respecto a la objetiva.

Pruebas y simulación


Figura 13. Boceto del brazo en RVIZ.
La simulación se centró en la visualización y validación cinemática de un brazo robótico. Teniendo en cuenta lo anterior, se tuvo un código principal URDF respecto al formato universal del formato descriptivo para definir la jerarquía de los eslabones, en el SolidWork fueron llamados “links” y las articulaciones que se nombraron “joints”.

Para la parte de la representación visual, cada eslabón está vinculado a una malla 3D que fue exportada en .stl desde el Solid.

Asimismo, se implementó un nodo llamado joint_state_publisher_gui, el cual permite manipular de forma independiente cada una de las articulaciones para verificar el rango de
movimiento | y | la | integridad | de | las
transformaciones de coordenadas.
Siguiendo la normativa de la Guía 1, los actuadores están limitados por software para no exceder los 2 rad/s en articulaciones rotacionales, garantizando la seguridad en el proceso de ensamble.
Por otro lado, el proceso de exportación y la configuración presentó varios desafíos técnicos un tanto críticos en los que se vieron:
- Incompatibilidad de versiones, pues el exportador del Solid generó una estructura de archivos basada en catkin que se manejaba en ROS1, lo que causó fallos de compilación en Ubuntu
24.04. Se tuvo que reestructurar el paquete manualmente a ament_cmake para ser compatible con ROS2.
- Errores en la jerarquía de orígenes, al inicio el brazo aparecía desplazado de su base debido a una mala interpretación de los sistemas de coordenadas globales en SolidWorks. Esto se corrigió editando el origen del joint_1 en el archivo .urdf para poder alinear los centros de masa.
- Gestión de dependencias y rutas, Ros2 presentó ciertas dificultades para localizar los archivos .urdf y las mallas dentro de las carpetas del sistema. La solución fue el uso de rutas absolutas y el mapeo de los directorios de instalación.

Además, para garantizar un comportamiento más realista, se realizó una fase de depuración de colisiones respecto a:
- Límites de rangos, se identificaron que las articulaciones como el joint_3 colisionaban con la estructura física del robot al superar ciertos ángulos.
- Ajuste de parámetros, al final se modificaron las etiquetas limit en el código fuente, en el .urdf, ajustando los valores de lower y upper en radianes para restringir el movimiento a zonas seguras de operación.

Boceto del brazo


Figura 14. Vista superior de la planta.

Se optó por un ensamblaje el cual estuviera directamente en una base cuadrada para poder poner la base rotatoria del brazo robótico y el dispensador de pimpones.
Por lo que, se buscó emplear el material MDF para la base cuadrada, la cual es la más grande, impresión 3D para la base circular en que irá el brazo, sin embargo, la parte de la tabla se diseñará para cortarlo en MDF. Esto con la finalidad de que sea un poco más fácil para desensamblar en algún caso de que se deba cambiar algún componente de los acoples o verificar las conexiones del motor y que las demás piezas internas se encuentren en correcto estado.
Regresando a la base cuadrada, se busca en el espaldar hacer una puerta para poder estar en constante observación respecto a la parte eléctrica, de igual manera, tener mayor facilidad a la hora de cambiar un determinado componente eléctrico y de igual forma, que los cables se encuentren bien conectados o si se llega a soltar alguno poder soldar y/o conectarlo sin tener que bajar todo el ensamblaje.

Respecto al dispensador de pimpones, se optó por hacerlo por medio de impresión 3D, ya que, se estaba mirando la posibilidad de construirlo en tubo pvc, pero para poder tener medidas exactas respecto a diámetro y al agarre que se le va a agregar en la parte inferior y en la parte de atrás para que no se suelte o quede al vacío.


Figura 15. Vista lateral izquierda de la planta.

Se puede observar el vacío que va a tener la base rotatoria, ya que, con eso evitamos que rose con la base cuadrada y tener mayores complicaciones a la hora de ponerlo a girar o que alguna esquirla o residuo llegue a generar cierto salto o fricción en la base.

Además, al dispensador de pelotas, pensamos en dejarle un hueco de 10 mm, donde caigan las pelotas y que para el robot le sea fácil agarrarlo evitando que el pimpón se corra para algún lado.


Figura 16. Vista frontal de la planta.

En la Figura 11, se puede ver directamente el Home del brazo, decidimos bajarlo de 5 ejes a 3, ya que era más dispendioso respecto a cálculos y control.

A su vez, se cambiaron las medidas de cada uno de los eslabones, ya que con las que se tenían antes quedaba muy pequeño el radio de giro, porque lo que, se podrían presentar complicaciones a la hora de dejar los pimpones en la bandeja, por ello, el largo del primer eslabón se dejó de 250 mm, del segundo 150 mm y el total de la garra es de 70 mm, con la finalidad de que tenga mayor espacio para los pimpones.

Respecto a la garra, buscamos una con la que se lograra tener 3 dedos de agarre pero que, por medio de una varilla corta se lograran subir los tres al mismo tiempo. En las prácticas pasadas se habían visto unas con agarre recto, pero el problema se iba a presentar en el momento de agarrar los pimpones debido a que se iban a deslizar, lo mismo, ocurría con un agarre de dos pinzas, considerando lo lisos que pueden llegar a ser esos.

Sin embargo, a pesar de tener un agarre con tres pinzas se está mirando la posibilidad de ponerle espuma en las puntas que sea más suave al momento de agarrar el pimpón y evitar cierto porcentaje del deslizamiento que se pueda llegar a ocasionar por su forma cónica y su textura lisa.

Plano Electricos


Figura 17. Plano eléctrico del sistema.

Para el control del sistema del robot contamos con una ESP32-WROOM como unidad de procesamiento el cual entregará la señal de PWM, direccionamiento de motores y lectura de encoders.

Como etapa de potencia se hizo uso de drives TB6612FNG los cuales nos permiten la bidireccionalidad, junto con eso, el driver permite corrientes de hasta 1A, un valor adecuado en en caso de sobrecarga para el robot.Este tipo de driver cuenta con niveles lógicos coincidentes con la ESP32 , su alimentación es de manera externa. Se hace uso de capacitores de 470 uF para la estabilización y reducción de picos durante los arranques de los motores.

Interfaz


Figura 18. Interfaz gráfica

La interfaz cuenta con ingreso de ángulos por medio de slider y campo de texto, se tiene un botón para confirmación de envío de ángulos y de emergencia el cual manda a home el robot en caso de problemas.
La inferzas tiene una relación con ros la cual le permita tener una visualización de la simulación directamente desde ROS2 , se muestran las coordenadas del efector final por medio de cinemática directa, se presenta la posición calculadora, el error de posición del efector.
Planos Mecánicos


Figura 19. Ensamblaje General Siguiendo las especificaciones de la Guía 1, se optó por una arquitectura antropomórfica (RRR) de 3 grados de libertad principales.

- Eslabones: | Diseñados | con
dimensiones optimizadas (L1=75 mm, L2 = 250 mm, L3=210 mm) para cubrir el área de trabajo establecida.
- Base | Rotativa: | Permite | el
posicionamiento angular para alcanzar los diferentes agujeros de la base de ensamble.
- Brazo y Antebrazo: Configuran el alcance vertical y radial necesario para tomar las piezas desde el repositorio y depositarlas con precisión.


Figura 20. Vista explosionada.

Control de velocidad del motor


Figura 21. Control de baja velocidad

De acuerdo con los requerimientos de la Guía 2, se implementó un sistema de control de bajo nivel para los motores DC con reductor seleccionado para el manipulador. La caracterización del sistema se realizó mediante una prueba de respuesta al escalón para determinar la dinámica de velocidad de las articulaciones.
La configuración del Sistema de Medición fue así:
- Resolución del Encoder: 408 pulsos por vuelta (PPR).
- Cuentas por vuelta: 4 (configuración en cuadratura para mayor precisión).

- Velocidad Nominal de Operación: 150 RPM.
A su vez, el análisis de la respuesta temporal fue el siguiente:
- Ganancia del sistema: Se determinó un valor de 0.9285, lo que indica la relación entre la magnitud del escalón de entrada y la velocidad final alcanzada en estado estacionario.
- Tiempo de establecimiento: El motor alcanza su velocidad final estable en aproximadamente 1.16 segundos. Este perfil de control asegura que la velocidad de las articulaciones rotacionales se mantenga estrictamente dentro del rango de 0 a 2 rad/s estipulado en las especificaciones de diseño.

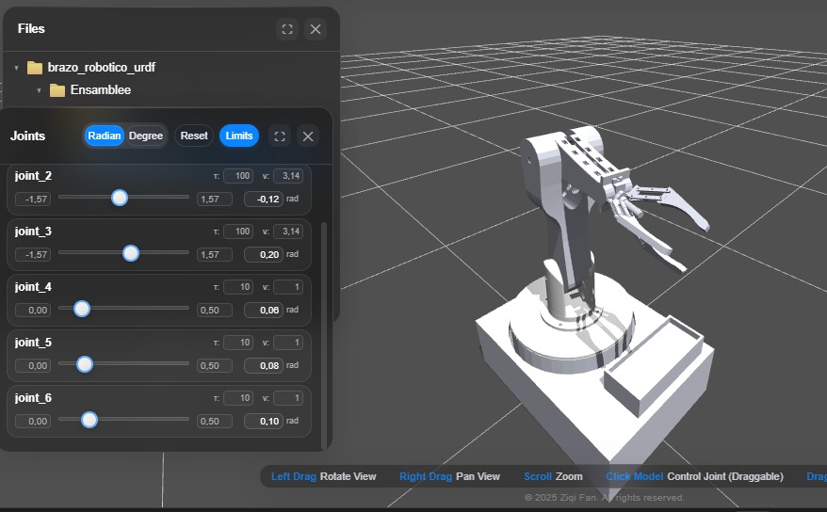
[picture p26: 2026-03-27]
Docs/Comprobación en otro programa (Robot Viewer).jpeg

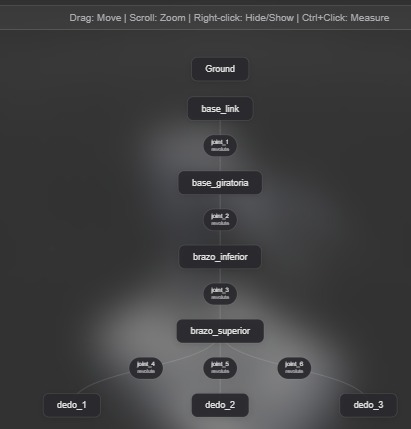
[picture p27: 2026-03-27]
Docs/Diagrama de bloques de Robot Viewer.jpeg

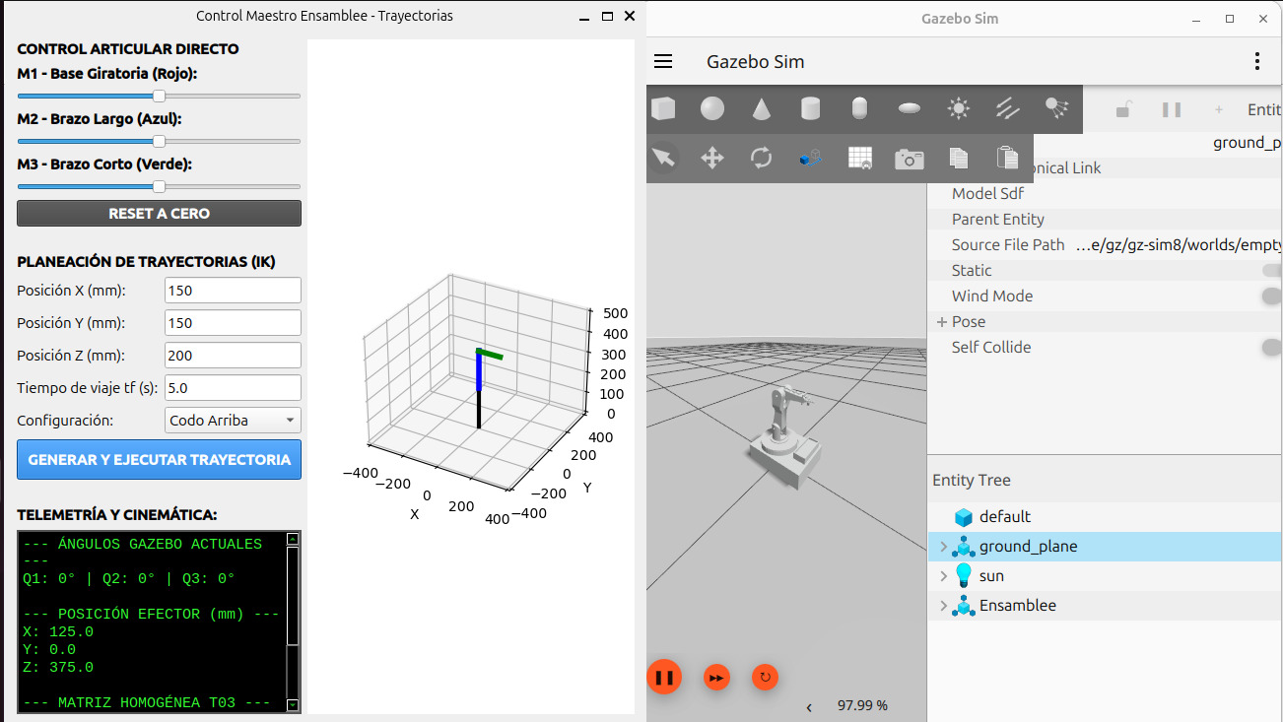
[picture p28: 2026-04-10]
Simulación/Simulacion_Gazebo_Interfaz_Home.jpg

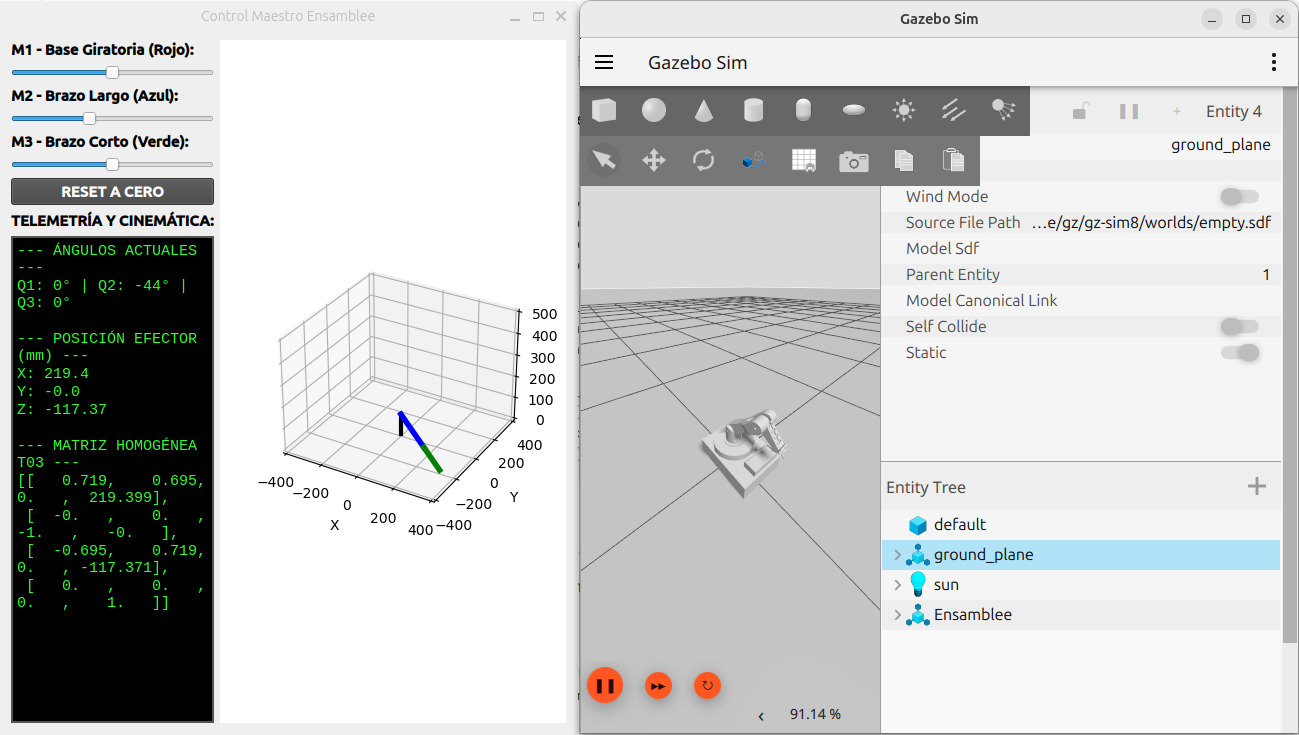
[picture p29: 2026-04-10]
Simulación/Simulacion_Gazebo_interfaz.jpeg

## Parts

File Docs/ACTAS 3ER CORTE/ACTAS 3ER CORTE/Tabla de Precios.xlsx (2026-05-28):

Cantidad | Atributo | Categoría | Estado | Encargado | Precios
1 | Base general | MDF | Finalizado | Laura | $15000 | Total | $983200
1 | Soporte para base pimpones | PETG | Finalizado | Carol | $2000 | Total Laura | $722600
1 | Planetario | PETG | Finalizado | Laura | $80000 | Total Carol | $167000
1 | Engranaje planetario | PETG | Finalizado | Laura | $35000 | Total Laura y Carol | $88600
1 | Base interior de planetario | MDF | Finalizado | Laura | $10000
1 | Acoples base - planetario | PETG | Finalizado | Laura | $1000
1 | Base superior planetario | MDF | Finalizado | Laura | $800
1 | Base pimpones | MDF | Finalizado | Laura | $3000
1 | Dispensador de pimpones | PETG | Finalizado | Laura y Carol | $8000
1 | Varilla | Acero | Finalizado | Laura y Carol | $10000
4 | Tornillos M4 | Acero | Finalizado | Laura | $800
1 | Correa HTD 3 210 | Varios | Finalizado | Laura | $18000
1 | Correa HTD 3 219 | Varios | Finalizado | Laura | $34000
1 | Servo motor ms90 | Varios | Finalizado | Carol | $13900
2 | Motor 90:1 | Varios | Finalizado | Laura | $260000
1 | Base para eslabones | PETG | Finalizado | Laura | $30000
1 | Eslabón inferior | PETG | Finalizado | Laura | $70000
1 | Eslabón superior 1 | PETG | Finalizado | Carol | $30000
1 | Pinza 1 | TPU | Finalizado | Carol | $8000
10 | Rodamientos 608RS | Acero | Finalizado | Laura y Carol | $46000
1 | Soporte motor pinza | PETG | Finalizado | Laura | $1000
1 | Motor de 150 rpm | Varios | Finalizado | Laura | $80000
10 | Tornillos M3 | Acero | Finalizado | Laura y Carol | $1500
10 | Acoples pinza | PETG | Finalizado | Laura | $500
1 | Bisagra | Acero | Finalizado | Laura | $2500
4 | Estiba | MDF | Finalizado | Laura | $8000
8 | Tornillos M2 | Acero | Finalizado | Carol | $500
1 | Engranaje 24 dientes HTD 3M | PETG | Finalizado | Carol | $2000
1 | Engranaje 20 dientes HTD 3M | PETG | Finalizado | Laura | $2000
1 | Engranaje 45 dientes HTD 3M | PETG | Finalizado | Laura | $5000
1 | Engranaje 48 dientes HTD 3M | PETG | Finalizado | Laura | $6000
10 | Ganchos | Acero | Finalizado | Laura | $5000
3 | Superbonder | Varios | Finalizado | Laura y Carol | $16800
4 | Limitadores | PETG | Finalizado | Laura | $3000
1 | PCB 1 | Varios | Finalizado | Carol | $40000
1 | PCB 2 | Varios | Finalizado | Laura | $55000
4 | Condensadores | Varios | Finalizado | Laura y Carol | $1400
4 | Regleta Pines macho macho | Varios | Finalizado | Carol | $2400
4 | Regleta pines macho hembra | Varios | Finalizado | Carol | $5600
3 | Borneras | Varios | Finalizado | Carol | $1500
2 | Drivers TB6612FNG | Varios | Finalizado | Carol | $23800
2 | IMU MPU6050 | Varios | Finalizado | Carol | $14900
2 | Jumper hembra hembra 30 cm | Varios | Finalizado | Carol | $5800
2 | Jumper hembra macho 30 cm | Varios | Finalizado | Carol | $5800
1 | Sensor hall KV003 | Varios | Finalizado | Carol | $5600
1 | Iman | Varios | Finalizado | Laura y Carol | $2400
1 | Organizador cable | Varios | Finalizado | Laura y Carol | $2500
1 | Jumper macho macho | Varios | Finalizado | Carol | $2900
2 | L | Varios | Finalizado | Laura | $2000
2 | Lijas 400 | Varios | Finalizado | Carol | $2300

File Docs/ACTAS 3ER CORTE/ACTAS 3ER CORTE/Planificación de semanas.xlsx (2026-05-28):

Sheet: Planificación de semanas
Objetivos | Prioridad | Propietario | Estado | Fecha de inicio | Fecha de finalización | Archivos relacionados | Notas
 | P0 |  | Retrasado
 | P1 |  | En peligro
 | P2 |  | En progreso
 | P3

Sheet: Hoja 1
Actividad | Tipo de actividad | Hora de inicio | Hora de finalización | Ubicación | Propietario | Notas
 | Actividad 1
 | Actividad 2
 | Actividad 3

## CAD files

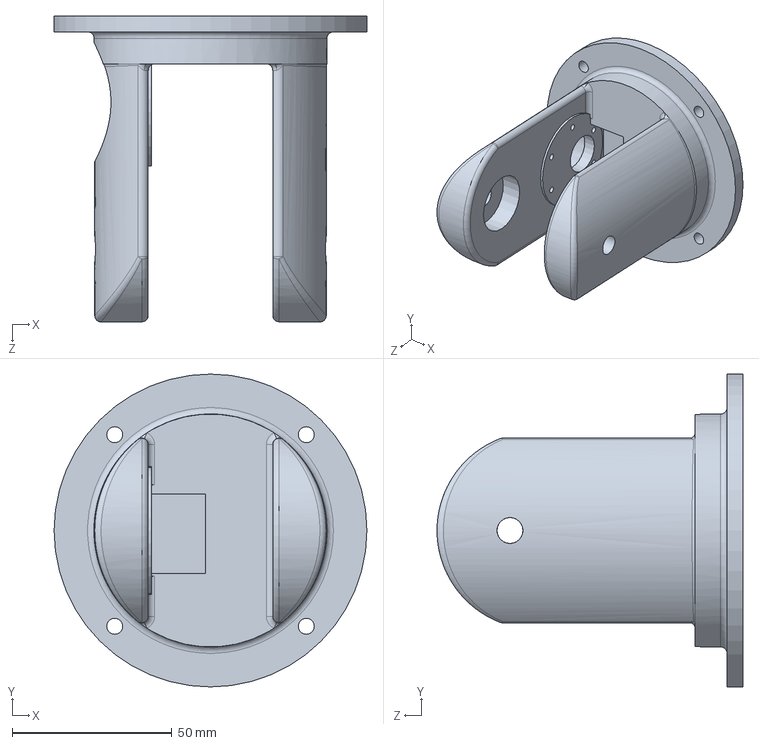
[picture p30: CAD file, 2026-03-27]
Hardware/Brazo General/Planetario/Base.SLDASM
98.0 x 98.0 x 95.9 mm

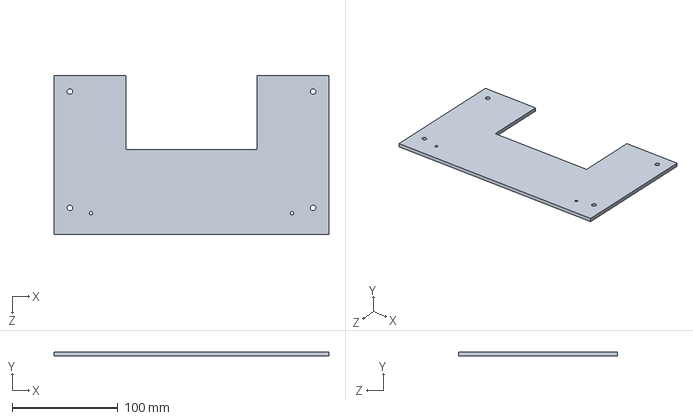
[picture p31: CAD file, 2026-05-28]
Bases Pinpones/Laurayyo.SLDPRT
260.0 x 4.00 x 150.0 mm

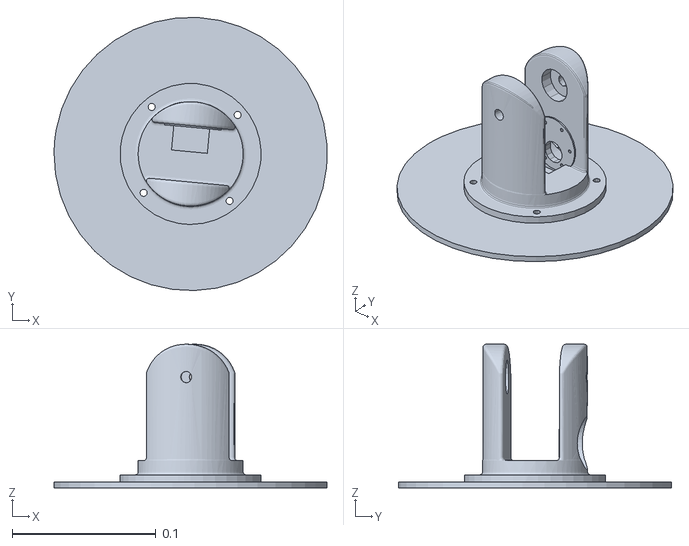
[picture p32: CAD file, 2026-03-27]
Hardware/Brazo General/brazo_robotico_urdf/Ensamblee/meshes/base_giratoria.STL
0.19 x 0.19 x 0.0999

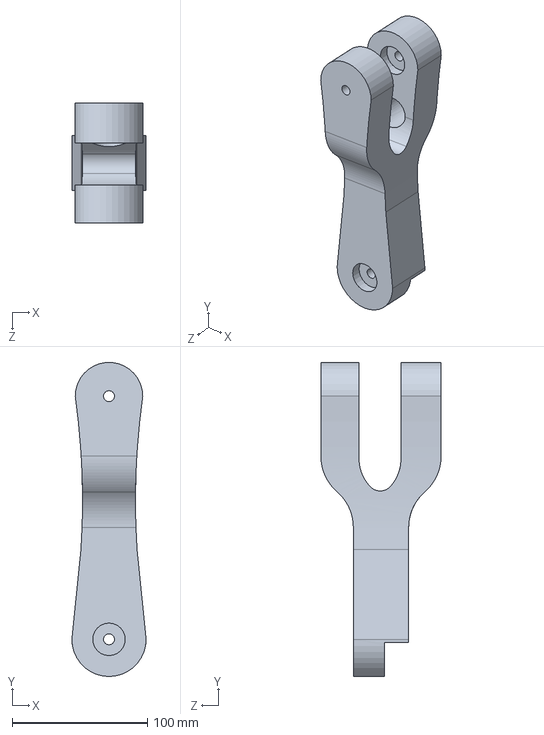
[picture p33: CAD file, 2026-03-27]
Hardware/Brazo General/Eslabon1.SLDPRT
55.0 x 232.4 x 89.0 mm

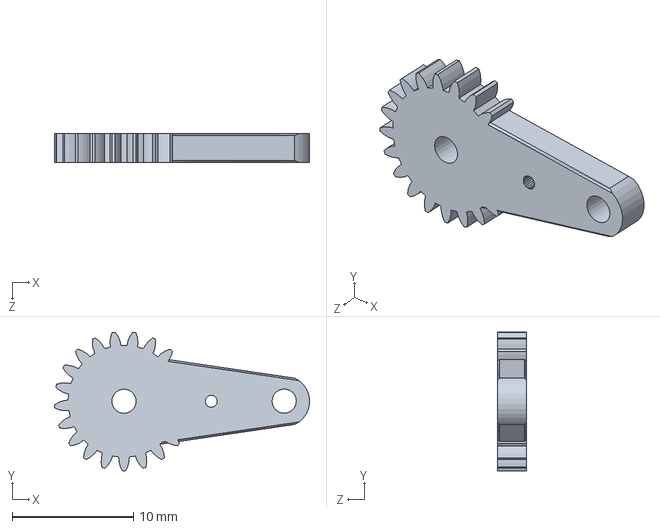
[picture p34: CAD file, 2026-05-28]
Hardware/Brazo General/Pinza Robot/Pinza2/Porsi2.SLDPRT
21.1 x 11.5 x 2.40 mm

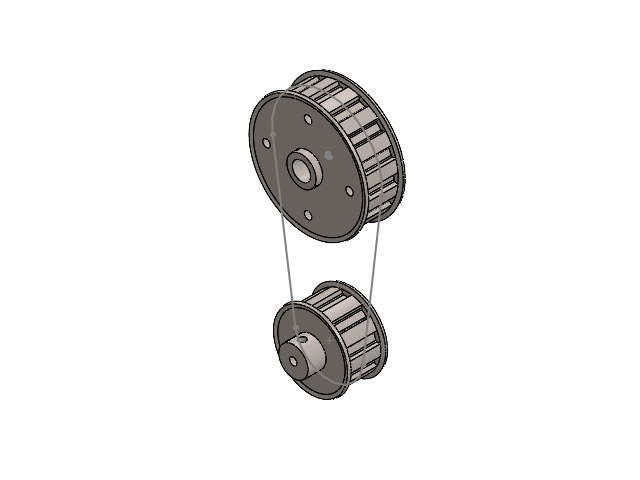
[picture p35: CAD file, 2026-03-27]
Hardware/Brazo General/jUNTURA.SLDASM
16L050-FS16-.5H1.5L0.3125N
10L050-FS10-.5H1.5L0.1250N

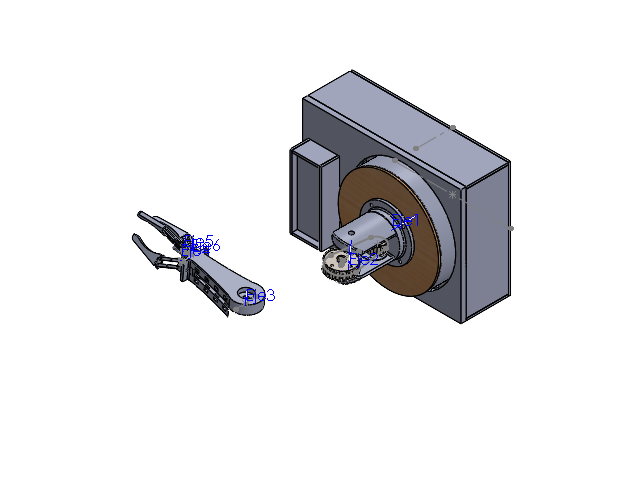
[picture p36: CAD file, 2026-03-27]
Hardware/Brazo General/Ensamblee.SLDASM
Base ancha
Base alta delantera con hueco
Base alta delantera
Base alta lateral x 2
Base ancha arriba
Tapa-planeta
Transmision Planetaria.step
SoporteTapaRodamiento
Rodamiento 628zz x 6
Base Rotatorio
Ajuste rodamiento
Delantera pinpon x 2
Lateral pinpon x 2
Base pinpones
BaseBajaPlaneta
BaseAltaPlanetario
BaseBasePlaneta x 2
BaseLateralPlaneta x 2
BasePrincipal
eslabonbrazo
Base2Ancha-pinpon x 2
Base2-pinpon x 2
Base2-Planchapinpon
servo.MG90S
soporte
tornillo
carritopinza
eslabonlargo x 12
eslabonchiqui x 3
gARRA x 3
16L050-FS16-.5H1.5L0.3125N
10L050-FS10-.5H1.5L0.1250N

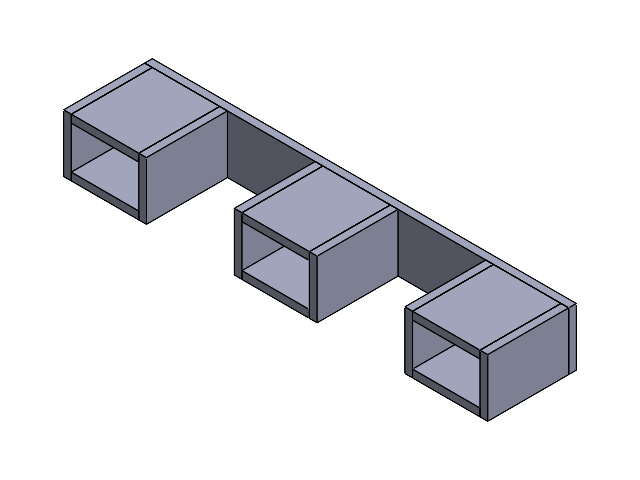
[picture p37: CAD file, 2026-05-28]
Hardware/Brazo General/Cuerpo Robot/Estiba lateral general.SLDASM
Estiba superior
Estiba ladito x 6
Estiba lateral x 6

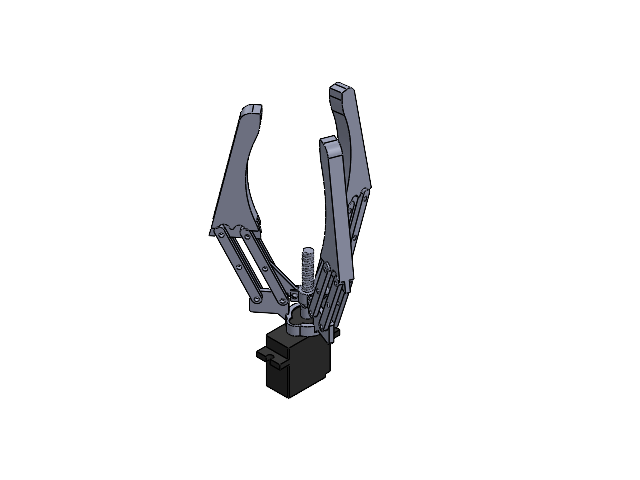
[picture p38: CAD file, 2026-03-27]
Hardware/Brazo General/Pinza Robot/Pinzarobotica/Pinza.SLDASM
servo.MG90S
soporte
tornillo
carritopinza
eslabonlargo x 12
eslabonchiqui x 3
gARRA x 3

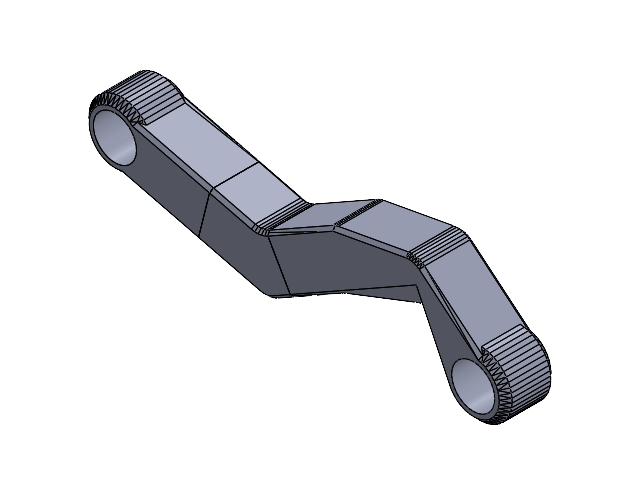
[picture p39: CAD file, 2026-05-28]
Hardware/Brazo General/Pinza Robot/Pinza2/Aver.SLDASM
levelito - copia
levelito - copia - copia
levelito - copia - copia - copia

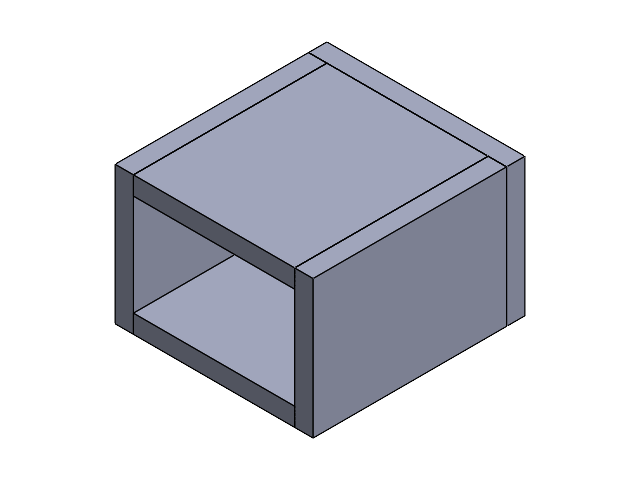
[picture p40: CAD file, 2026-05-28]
Hardware/Brazo General/Cuerpo Robot/Estiba central general.SLDASM
Estiba baja
Estiba ladito x 2
Estiba lateral x 2

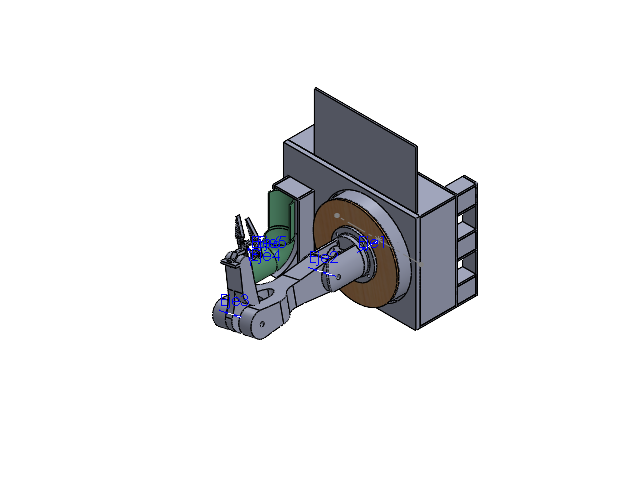
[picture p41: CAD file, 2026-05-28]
Hardware/Brazo General/Cuerpo Robot/Ensamble General.SLDASM
Base ancha
Base alta delantera con hueco
Base alta delantera
Base alta lateral x 2
Base ancha arriba
Tapa-planeta
Transmision Planetaria.step
SoporteTapaRodamiento
Rodamiento 628zz x 4
Base Rotatorio
Ajuste rodamiento
Delantera pinpon x 2
Lateral pinpon x 2
Base pinpones
Tubito Pimpones
Tubito Pimpones1 - copia
BaseBajaPlaneta
BaseAltaPlanetario
BaseBasePlaneta x 2
BaseLateralPlaneta x 2
BasePrincipal
Eslabon1
Base2Ancha-pinpon x 2
Base2-pinpon x 2
Base2-Planchapinpon
eslabonbrazo
Soporte pinza 1 x 2
Pinza1 x 2
levelito x 2
Base general
servo.MG90S
eslabonchiqui
Seguro1 x 4
Tapa soporte
Seguro2
Seguro3
Porsi
Porsi2
Estiba superior x 2
Estiba ladito x 16
Estiba lateral x 16
Estiba baja x 2
Soporte motor
Soporte pinpon

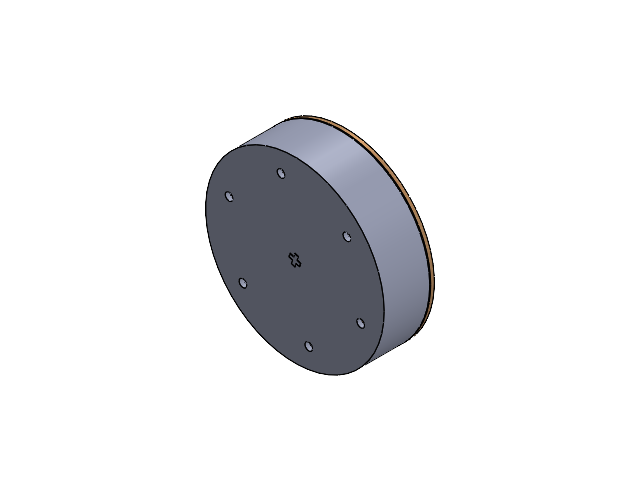
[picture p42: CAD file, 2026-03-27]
Hardware/Brazo General/Planetario/PlanetarioBase.SLDASM
Tapa-planeta
Transmision Planetaria.step
SoporteTapaRodamiento
Rodamiento 628zz x 4
Base Rotatorio
Ajuste rodamiento

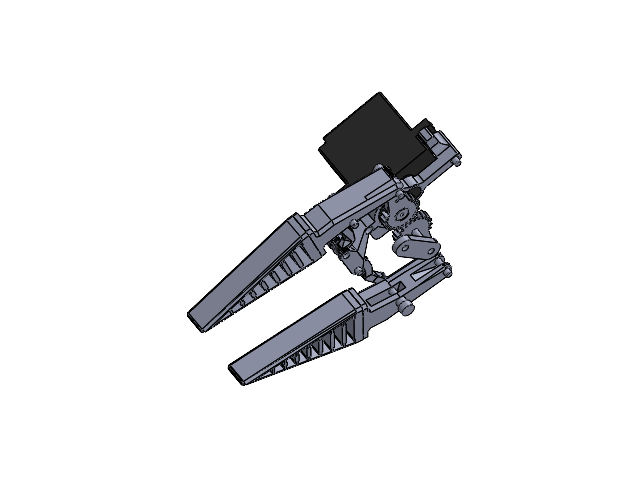
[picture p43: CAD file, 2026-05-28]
Hardware/Brazo General/Pinza Robot/Pinza2/PINZAAAAAAAAA.SLDASM
Soporte pinza 1 x 2
Pinza1 x 2
levelito
Base general
servo.MG90S
eslabonchiqui
Seguro1 x 4
Tapa soporte
Seguro2
Seguro3
Porsi
Porsi2
levelito - copia
levelito - copia - copia
levelito - copia - copia - copia

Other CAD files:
Hardware/Brazo General/Planetario/Transmision Planetaria (Ensamblaje).SLDASM
Hardware/Brazo General/Cuerpo Robot/Ensamblaje1.SLDASM
Hardware/Brazo General/Pinza Robot/Pinza2/Porsi.SLDPRT.SLDASM
Hardware/Brazo General/Cuerpo Robot/BasePrincipal.SLDPRT
Bases Pinpones/Grupocarlitos.DXF
Bases Pinpones/Grupocarlitos.SLDPRT
Bases Pinpones/Laurayyo.DXF
Bases Pinpones/Segundogrupo.DXF
Bases Pinpones/Segundogrupo.SLDPRT
Hardware/Brazo General/Cuerpo Robot/Base alta delantera con hueco.SLDPRT
Hardware/Brazo General/Cuerpo Robot/Base alta delantera.SLDPRT
Hardware/Brazo General/Cuerpo Robot/Base alta lateral.SLDPRT
Hardware/Brazo General/Cuerpo Robot/Base ancha arriba.SLDPRT
Hardware/Brazo General/Cuerpo Robot/Base ancha.SLDPRT
Hardware/Brazo General/Cuerpo Robot/Base pinpones.SLDPRT
Hardware/Brazo General/Cuerpo Robot/Base2-Planchapinpon.SLDPRT
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

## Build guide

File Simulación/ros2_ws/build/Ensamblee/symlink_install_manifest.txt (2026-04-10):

/home/laura/ros2_ws/install/Ensamblee/share/Ensamblee/launch/display.launch
/home/laura/ros2_ws/install/Ensamblee/share/Ensamblee/launch/display.launch.py
/home/laura/ros2_ws/install/Ensamblee/share/Ensamblee/launch/gazebo.launch
/home/laura/ros2_ws/install/Ensamblee/share/Ensamblee/launch/gazebo.launch.py
/home/laura/ros2_ws/install/Ensamblee/share/Ensamblee/meshes/base_giratoria.STL
/home/laura/ros2_ws/install/Ensamblee/share/Ensamblee/meshes/base_link.STL
/home/laura/ros2_ws/install/Ensamblee/share/Ensamblee/meshes/brazo_inferior.STL
/home/laura/ros2_ws/install/Ensamblee/share/Ensamblee/meshes/brazo_superior.STL
/home/laura/ros2_ws/install/Ensamblee/share/Ensamblee/meshes/dedo_1.STL
/home/laura/ros2_ws/install/Ensamblee/share/Ensamblee/meshes/dedo_2.STL
/home/laura/ros2_ws/install/Ensamblee/share/Ensamblee/meshes/dedo_3.STL
/home/laura/ros2_ws/install/Ensamblee/share/Ensamblee/urdf/Ensamblee.csv
/home/laura/ros2_ws/install/Ensamblee/share/Ensamblee/urdf/Ensamblee.urdf
/home/laura/ros2_ws/install/Ensamblee/share/ament_index/resource_index/package_run_dependencies/Ensamblee
/home/laura/ros2_ws/install/Ensamblee/share/ament_index/resource_index/parent_prefix_path/Ensamblee
/home/laura/ros2_ws/install/Ensamblee/share/Ensamblee/environment/ament_prefix_path.sh
/home/laura/ros2_ws/install/Ensamblee/share/Ensamblee/environment/ament_prefix_path.dsv
/home/laura/ros2_ws/install/Ensamblee/share/Ensamblee/environment/path.sh
/home/laura/ros2_ws/install/Ensamblee/share/Ensamblee/environment/path.dsv
/home/laura/ros2_ws/install/Ensamblee/share/Ensamblee/local_setup.bash
/home/laura/ros2_ws/install/Ensamblee/share/Ensamblee/local_setup.sh
/home/laura/ros2_ws/install/Ensamblee/share/Ensamblee/local_setup.zsh
/home/laura/ros2_ws/install/Ensamblee/share/Ensamblee/local_setup.dsv
/home/laura/ros2_ws/install/Ensamblee/share/Ensamblee/package.dsv
/home/laura/ros2_ws/install/Ensamblee/share/ament_index/resource_index/packages/Ensamblee
/home/laura/ros2_ws/install/Ensamblee/share/Ensamblee/cmake/EnsambleeConfig.cmake
/home/laura/ros2_ws/install/Ensamblee/share/Ensamblee/cmake/EnsambleeConfig-version.cmake
/home/laura/ros2_ws/install/Ensamblee/share/Ensamblee/package.xml

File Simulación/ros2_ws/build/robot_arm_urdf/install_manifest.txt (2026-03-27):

/home/laura/ros2_ws/install/robot_arm_urdf/share/robot_arm_urdf/config/joint_names_robot_arm_urdf.yaml
/home/laura/ros2_ws/install/robot_arm_urdf/share/robot_arm_urdf/launch/gazebo.launch
/home/laura/ros2_ws/install/robot_arm_urdf/share/robot_arm_urdf/launch/display.launch
/home/laura/ros2_ws/install/robot_arm_urdf/share/robot_arm_urdf/meshes/link_4.STL
/home/laura/ros2_ws/install/robot_arm_urdf/share/robot_arm_urdf/meshes/link_5.STL
/home/laura/ros2_ws/install/robot_arm_urdf/share/robot_arm_urdf/meshes/link_1.STL
/home/laura/ros2_ws/install/robot_arm_urdf/share/robot_arm_urdf/meshes/base_link.STL
/home/laura/ros2_ws/install/robot_arm_urdf/share/robot_arm_urdf/meshes/link_3.STL
/home/laura/ros2_ws/install/robot_arm_urdf/share/robot_arm_urdf/meshes/link_7.STL
/home/laura/ros2_ws/install/robot_arm_urdf/share/robot_arm_urdf/meshes/link_2.STL
/home/laura/ros2_ws/install/robot_arm_urdf/share/robot_arm_urdf/meshes/link_6.STL
/home/laura/ros2_ws/install/robot_arm_urdf/share/robot_arm_urdf/urdf/robot_arm_urdf.csv
/home/laura/ros2_ws/install/robot_arm_urdf/share/robot_arm_urdf/urdf/robot_arm_urdf.urdf
/home/laura/ros2_ws/install/robot_arm_urdf/share/ament_index/resource_index/package_run_dependencies/robot_arm_urdf
/home/laura/ros2_ws/install/robot_arm_urdf/share/ament_index/resource_index/parent_prefix_path/robot_arm_urdf
/home/laura/ros2_ws/install/robot_arm_urdf/share/robot_arm_urdf/environment/ament_prefix_path.sh
/home/laura/ros2_ws/install/robot_arm_urdf/share/robot_arm_urdf/environment/ament_prefix_path.dsv
/home/laura/ros2_ws/install/robot_arm_urdf/share/robot_arm_urdf/environment/path.sh
/home/laura/ros2_ws/install/robot_arm_urdf/share/robot_arm_urdf/environment/path.dsv
/home/laura/ros2_ws/install/robot_arm_urdf/share/robot_arm_urdf/local_setup.bash
/home/laura/ros2_ws/install/robot_arm_urdf/share/robot_arm_urdf/local_setup.sh
/home/laura/ros2_ws/install/robot_arm_urdf/share/robot_arm_urdf/local_setup.zsh
/home/laura/ros2_ws/install/robot_arm_urdf/share/robot_arm_urdf/local_setup.dsv
/home/laura/ros2_ws/install/robot_arm_urdf/share/robot_arm_urdf/package.dsv
/home/laura/ros2_ws/install/robot_arm_urdf/share/ament_index/resource_index/packages/robot_arm_urdf
/home/laura/ros2_ws/install/robot_arm_urdf/share/robot_arm_urdf/cmake/robot_arm_urdfConfig.cmake
/home/laura/ros2_ws/install/robot_arm_urdf/share/robot_arm_urdf/cmake/robot_arm_urdfConfig-version.cmake
/home/laura/ros2_ws/install/robot_arm_urdf/share/robot_arm_urdf/package.xml

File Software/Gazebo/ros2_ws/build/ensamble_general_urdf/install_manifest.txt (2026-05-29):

/home/laura/ros2_ws/install/ensamble_general_urdf/share/ensamble_general_urdf/launch/display.launch.py
/home/laura/ros2_ws/install/ensamble_general_urdf/share/ensamble_general_urdf/launch/gazebo.launch.py
/home/laura/ros2_ws/install/ensamble_general_urdf/share/ensamble_general_urdf/meshes/soporte_pinza.STL
/home/laura/ros2_ws/install/ensamble_general_urdf/share/ensamble_general_urdf/meshes/base_giratoria.STL
/home/laura/ros2_ws/install/ensamble_general_urdf/share/ensamble_general_urdf/meshes/dedo_2.STL
/home/laura/ros2_ws/install/ensamble_general_urdf/share/ensamble_general_urdf/meshes/eslabon_superior.STL
/home/laura/ros2_ws/install/ensamble_general_urdf/share/ensamble_general_urdf/meshes/eslabon_inferior.STL
/home/laura/ros2_ws/install/ensamble_general_urdf/share/ensamble_general_urdf/meshes/base.STL
/home/laura/ros2_ws/install/ensamble_general_urdf/share/ensamble_general_urdf/meshes/dedo_1.STL
/home/laura/ros2_ws/install/ensamble_general_urdf/share/ensamble_general_urdf/urdf/ensamble_general_urdf.csv
/home/laura/ros2_ws/install/ensamble_general_urdf/share/ensamble_general_urdf/urdf/ensamble_general_urdf.urdf
/home/laura/ros2_ws/install/ensamble_general_urdf/share/ament_index/resource_index/package_run_dependencies/ensamble_general_urdf
/home/laura/ros2_ws/install/ensamble_general_urdf/share/ament_index/resource_index/parent_prefix_path/ensamble_general_urdf
/home/laura/ros2_ws/install/ensamble_general_urdf/share/ensamble_general_urdf/environment/ament_prefix_path.sh
/home/laura/ros2_ws/install/ensamble_general_urdf/share/ensamble_general_urdf/environment/ament_prefix_path.dsv
/home/laura/ros2_ws/install/ensamble_general_urdf/share/ensamble_general_urdf/environment/path.sh
/home/laura/ros2_ws/install/ensamble_general_urdf/share/ensamble_general_urdf/environment/path.dsv
/home/laura/ros2_ws/install/ensamble_general_urdf/share/ensamble_general_urdf/local_setup.bash
/home/laura/ros2_ws/install/ensamble_general_urdf/share/ensamble_general_urdf/local_setup.sh
/home/laura/ros2_ws/install/ensamble_general_urdf/share/ensamble_general_urdf/local_setup.zsh
/home/laura/ros2_ws/install/ensamble_general_urdf/share/ensamble_general_urdf/local_setup.dsv
/home/laura/ros2_ws/install/ensamble_general_urdf/share/ensamble_general_urdf/package.dsv
/home/laura/ros2_ws/install/ensamble_general_urdf/share/ament_index/resource_index/packages/ensamble_general_urdf
/home/laura/ros2_ws/install/ensamble_general_urdf/share/ensamble_general_urdf/cmake/ensamble_general_urdfConfig.cmake
/home/laura/ros2_ws/install/ensamble_general_urdf/share/ensamble_general_urdf/cmake/ensamble_general_urdfConfig-version.cmake
/home/laura/ros2_ws/install/ensamble_general_urdf/share/ensamble_general_urdf/package.xml

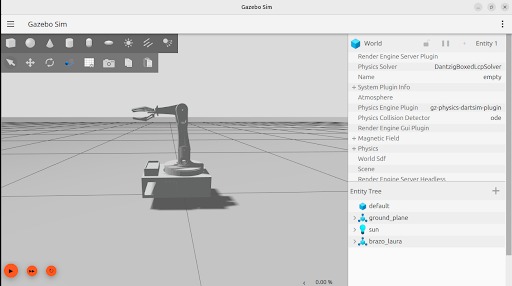
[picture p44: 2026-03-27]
Docs/Ensamblaje Home Gazebo.jpeg

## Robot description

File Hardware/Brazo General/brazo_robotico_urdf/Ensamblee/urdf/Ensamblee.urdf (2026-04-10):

<?xml version="1.0" encoding="utf-8"?>
<robot name="Ensamblee">

  <link name="world"/>
  <joint name="fixed_base" type="fixed">
    <parent link="world"/>
    <child link="base_link"/>
    <origin xyz="0 0 0" rpy="0 0 0"/>
  </joint>

  <link name="base_link">
    <inertial>
      <origin xyz="0.035133 0.0010982 0.059578" rpy="0 0 0" />
      <mass value="1.6222" />
      <inertia ixx="0.0057091" ixy="0.00016017" ixz="-1.9562E-07" iyy="0.0078069" iyz="7.9795E-07" izz="0.01293" />
    </inertial>
    <visual>
      <origin xyz="0 0 0" rpy="0 0 0" />
      <geometry><mesh filename="model://Ensamblee/meshes/base_link.STL" /></geometry>
      <material name="gris_azulado"><color rgba="0.79216 0.81961 0.93333 1" /></material>
    </visual>
    <collision>
      <origin xyz="0 0 0" rpy="0 0 0" />
      <geometry><mesh filename="model://Ensamblee/meshes/base_link.STL" /></geometry>
    </collision>
  </link>

  <link name="base_giratoria">
    <inertial>
      <origin xyz="-0.00012545 -0.0015041 0.14037" rpy="0 0 0" />
      <mass value="0.27811" />
      <inertia ixx="0.00049658" ixy="-4.0519E-06" ixz="-2.3048E-07" iyy="0.00045443" iyz="-3.5467E-06" izz="0.00066548" />
    </inertial>
    <visual>
      <origin xyz="0 0 0" rpy="0 0 0" />
      <geometry><mesh filename="model://Ensamblee/meshes/base_giratoria.STL" /></geometry>
      <material name="blanco"><color rgba="1 1 1 1" /></material>
    </visual>
    <collision>
      <origin xyz="0 0 0" rpy="0 0 0" />
      <geometry><mesh filename="model://Ensamblee/meshes/base_giratoria.STL" /></geometry>
    </collision>
  </link>
  <joint name="joint_1" type="revolute">
    <origin xyz="0 0 0" rpy="0 0 0" />
    <parent link="base_link" /><child link="base_giratoria" /><axis xyz="0 0 1" />
    <limit lower="-3.14" upper="3.14" effort="100" velocity="3.14" />
    <dynamics damping="10.0" friction="1.0"/>
  </joint>

  <link name="brazo_inferior">
    <inertial>
      <origin xyz="0.10277 -0.010539 0.0045472" rpy="0 0 0" />
      <mass value="0.41319" />
      <inertia ixx="0.00031344" ixy="0.00016033" ixz="4.1036E-05" iyy="0.0018606" iyz="-4.2071E-06" izz="0.0017287" />
    </inertial>
    <visual>
      <origin xyz="0 0 0" rpy="0 0 0" />
      <geometry><mesh filename="model://Ensamblee/meshes/brazo_inferior.STL" /></geometry>
      <material name="gris_azulado"><color rgba="0.79216 0.81961 0.93333 1" /></material>
    </visual>
    <collision>
      <origin xyz="0 0 0" rpy="0 0 0" />
      <geometry><mesh filename="model://Ensamblee/meshes/brazo_inferior.STL" /></geometry>
    </collision>
  </link>
  <joint name="joint_2" type="revolute">
    <origin xyz="0.00032733 0.0034847 0.1945" rpy="1.6645 -1.5708 0" />
    <parent link="base_giratoria" /><child link="brazo_inferior" /><axis xyz="0 0 -1" />
    <limit lower="-1.57" upper="1.57" effort="100" velocity="3.14" />
    <dynamics damping="15.0" friction="2.0"/>
  </joint>

  <link name="brazo_superior">
    <inertial>
      <origin xyz="0.049945 -0.003032 0.0023765" rpy="0 0 0" />
      <mass value="0.13139" />
      <inertia ixx="2.7543E-05" ixy="6.4343E-06" ixz="1.1157E-05" iyy="0.00016188" iyz="-6.8148E-07" izz="0.00016442" />
    </inertial>
    <visual>
      <origin xyz="0 0 0" rpy="0 0 0" />
      <geometry><mesh filename="model://Ensamblee/meshes/brazo_superior.STL" /></geometry>
      <material name="gris_azulado"><color rgba="0.79216 0.81961 0.93333 1" /></material>
    </visual>
    <collision>
      <origin xyz="0 0 0" rpy="0 0 0" />
      <geometry><mesh filename="model://Ensamblee/meshes/brazo_superior.STL" /></geometry>
    </collision>
  </link>
  <joint name="joint_3" type="revolute">
    <origin xyz="0.17906 -0.018361 0.00076231" rpy="0 0 -1.5708" />
    <parent link="brazo_inferior" /><child link="brazo_superior" /><axis xyz="0 0 -1" />
    <limit lower="-1.57" upper="1.57" effort="100" velocity="3.14" />
    <dynamics damping="10.0" friction="1.0"/>
  </joint>

  <link name="ensamblaje_corto">
    <inertial><mass value="0.05"/><inertia ixx="1e-4" ixy="0" ixz="0" iyy="1e-4" iyz="0" izz="1e-4"/></inertial>
    <visual>
      <origin xyz="0 0 0" rpy="0 0 0" />
      <geometry><mesh filename="model://Ensamblee/meshes/ensamblaje_corto.STL" /></geometry>
      <material name="gris_oscuro"><color rgba="0.3 0.3 0.3 1" /></material>
    </visual>
    <collision>
      <geometry><mesh filename="model://Ensamblee/meshes/ensamblaje_corto.STL" /></geometry>
    </collision>
  </link>
  <joint name="joint_corto" type="fixed">
    <origin xyz="0.125 0 0" rpy="0 0 0" />
    <parent link="brazo_superior" /><child link="ensamblaje_corto" />
  </joint>

  <link name="dedo_1">
    <visual><geometry><mesh filename="model://Ensamblee/meshes/dedo_1.STL"/></geometry><material name="blanco"/></visual>
  </link>
  <joint name="joint_4" type="revolute">
    <origin xyz="0.03 -0.01 0.01" rpy="2.25 0 0" /><parent link="ensamblaje_corto" /><child link="dedo_1" /><axis xyz="0 0 1" /><limit lower="0" upper="0.5" effort="10" velocity="1" />
  </joint>

  <link name="dedo_2">
    <visual><geometry><mesh filename="model://Ensamblee/meshes/dedo_2.STL"/></geometry><material name="blanco"/></visual>
  </link>
  <joint name="joint_5" type="revolute">
    <origin xyz="0.03 -0.01 -0.01" rpy="-1.94 0 0" /><parent link="ensamblaje_corto" /><child link="dedo_2" /><axis xyz="0 0 1" /><limit lower="0" upper="0.5" effort="10" velocity="1" />
  </joint>

  <link name="dedo_3">
    <visual><geometry><mesh filename="model://Ensamblee/meshes/dedo_3.STL"/></geometry><material name="blanco"/></visual>
  </link>
  <joint name="joint_6" type="revolute">
    <origin xyz="0.03 0.02 0" rpy="0.15 0 0" /><parent link="ensamblaje_corto" /><child link="dedo_3" /><axis xyz="0 0 1" /><limit lower="0" upper="0.5" effort="10" velocity="1" />
  </joint>

  <gazebo>
    <plugin filename="gz-sim-joint-state-publisher-system" name="gz::sim::systems::JointStatePublisher">
      <joint_name>joint_1</joint_name><joint_name>joint_2</joint_name><joint_name>joint_3</joint_name>
    </plugin>
    <plugin filename="gz-sim-joint-position-controller-system" name="gz::sim::systems::JointPositionController">
      <joint_name>joint_1</joint_name><topic>/model/Ensamblee/joint/joint_1/cmd_pos</topic>
      <p_gain>1000</p_gain><d_gain>50</d_gain> </plugin>
    <plugin filename="gz-sim-joint-position-controller-system" name="gz::sim::systems::JointPositionController">
      <joint_name>joint_2</joint_name><topic>/model/Ensamblee/joint/joint_2/cmd_pos</topic>
      <p_gain>2000</p_gain><d_gain>100</d_gain>
    </plugin>
    <plugin filename="gz-sim-joint-position-controller-system" name="gz::sim::systems::JointPositionController">
      <joint_name>joint_3</joint_name><topic>/model/Ensamblee/joint/joint_3/cmd_pos</topic>
      <p_gain>1000</p_gain><d_gain>50</d_gain>
    </plugin>
  </gazebo>

</robot>

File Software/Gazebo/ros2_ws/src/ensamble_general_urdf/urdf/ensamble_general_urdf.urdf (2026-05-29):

<?xml version="1.0" encoding="utf-8"?>
<robot name="ensamble_general_urdf">

  <link name="world"/>
  
  <joint name="fixed_base" type="fixed">
    <parent link="world"/>
    <child link="base"/>
    <origin xyz="0 0 0" rpy="0 0 0"/>
  </joint>

  <link name="base">
    <inertial>
      <origin xyz="0.010178 0.038491 -0.014831" rpy="0 0 0" />
      <mass value="2.0149" />
      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
    </inertial>
    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
  </link>

  <link name="base_giratoria">
    <inertial>
      <origin xyz="0.00033752 -0.001741 0.072369" rpy="0 0 0" />
      <mass value="0.27811" />
      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
    </inertial>
    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
  </link>

  <joint name="joint_1" type="revolute">
    <origin xyz="0 0 0" rpy="0 0 0" />
    <parent link="base" />
    <child link="base_giratoria" />
    <axis xyz="0 0 1" />
    <limit lower="-3.142" upper="3.142" effort="100" velocity="2" />
    <dynamics damping="10.0" friction="1.0"/>
  </joint>

  <link name="eslabon_inferior">
    <inertial>
      <origin xyz="1.5352E-05 -0.10329 -0.0044136" rpy="0 0 0" />
      <mass value="0.41558" />
      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
    </inertial>
    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
  </link>

  <joint name="joint_2" type="revolute">
    <origin xyz="-0.000747 0.0031495 0.1265" rpy="-1.5708 0 0.21508" />
    <parent link="base_giratoria" />
    <child link="eslabon_inferior" />
    <axis xyz="0 0 1" />
    <limit lower="-1.57" upper="1.57" effort="100" velocity="2" />
    <dynamics damping="15.0" friction="2.0"/>
  </joint>

  <link name="eslabon_superior">
    <inertial>
      <origin xyz="0.045973 0.0091436 0.0037482" rpy="0 0 0" />
      <mass value="0.10171" />
      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
    </inertial>
    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
  </link>

  <joint name="joint_3" type="revolute">
    <origin xyz="2.6757E-05 -0.18 -0.0027601" rpy="0 0.075039 -0.10127" />
    <parent link="eslabon_inferior" />
    <child link="eslabon_superior" />
    <axis xyz="-0.074969 0 0.99719" />
    <limit lower="0" upper="1.57" effort="100" velocity="2" />
    <dynamics damping="10.0" friction="1.0"/>
  </joint>

  <link name="soporte_pinza">
    <inertial>
      <origin xyz="0.013114 0.0050536 0.0047901" rpy="0 0 0" />
      <mass value="0.012112" />
      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
    </inertial>
    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
  </link>

  <joint name="joint_4" type="fixed">
    <origin xyz="0.093465 0.04227 0.0047203" rpy="-1.4926 -0.33132 -1.4222" />
    <parent link="eslabon_superior" />
    <child link="soporte_pinza" />
    <axis xyz="0 0 0" />
    <limit lower="0" upper="0" effort="100" velocity="2" />
  </joint>

  <link name="dedo_1">
    <inertial>
      <origin xyz="0.022829 -0.0090327 0.0026146" rpy="0 0 0" />
      <mass value="0.0031986" />
      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
    </inertial>
    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
  </link>

  <joint name="joint_5" type="revolute">
    <origin xyz="-0.0065469 0.0092105 0.0059454" rpy="-1.5708 -1.4417 -1.2515" />
    <parent link="soporte_pinza" />
    <child link="dedo_1" />
    <axis xyz="0 0 -1" />
    <limit lower="0" upper="0.8" effort="10" velocity="1" />
    <dynamics damping="1.0" friction="1.0"/>
  </joint>

  <link name="dedo_2">
    <inertial>
      <origin xyz="0.024055 0.012408 -0.0014123" rpy="0 0 0" />
      <mass value="0.0031653" />
      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
    </inertial>
    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
  </link>

  <joint name="joint_6" type="revolute">
    <origin xyz="-0.001258 -0.0004159 0.0058" rpy="-1.5708 -1.305 -1.2515" />
    <parent link="soporte_pinza" />
    <child link="dedo_2" />
    <axis xyz="0 0 -1" />
    <limit lower="-0.8" upper="0" effort="10" velocity="1" />
    <dynamics damping="1.0" friction="1.0"/>
  </joint>

  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
</robot>

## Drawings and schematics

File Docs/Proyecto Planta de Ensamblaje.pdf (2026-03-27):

## Nodo Maestro (Equipo 0)

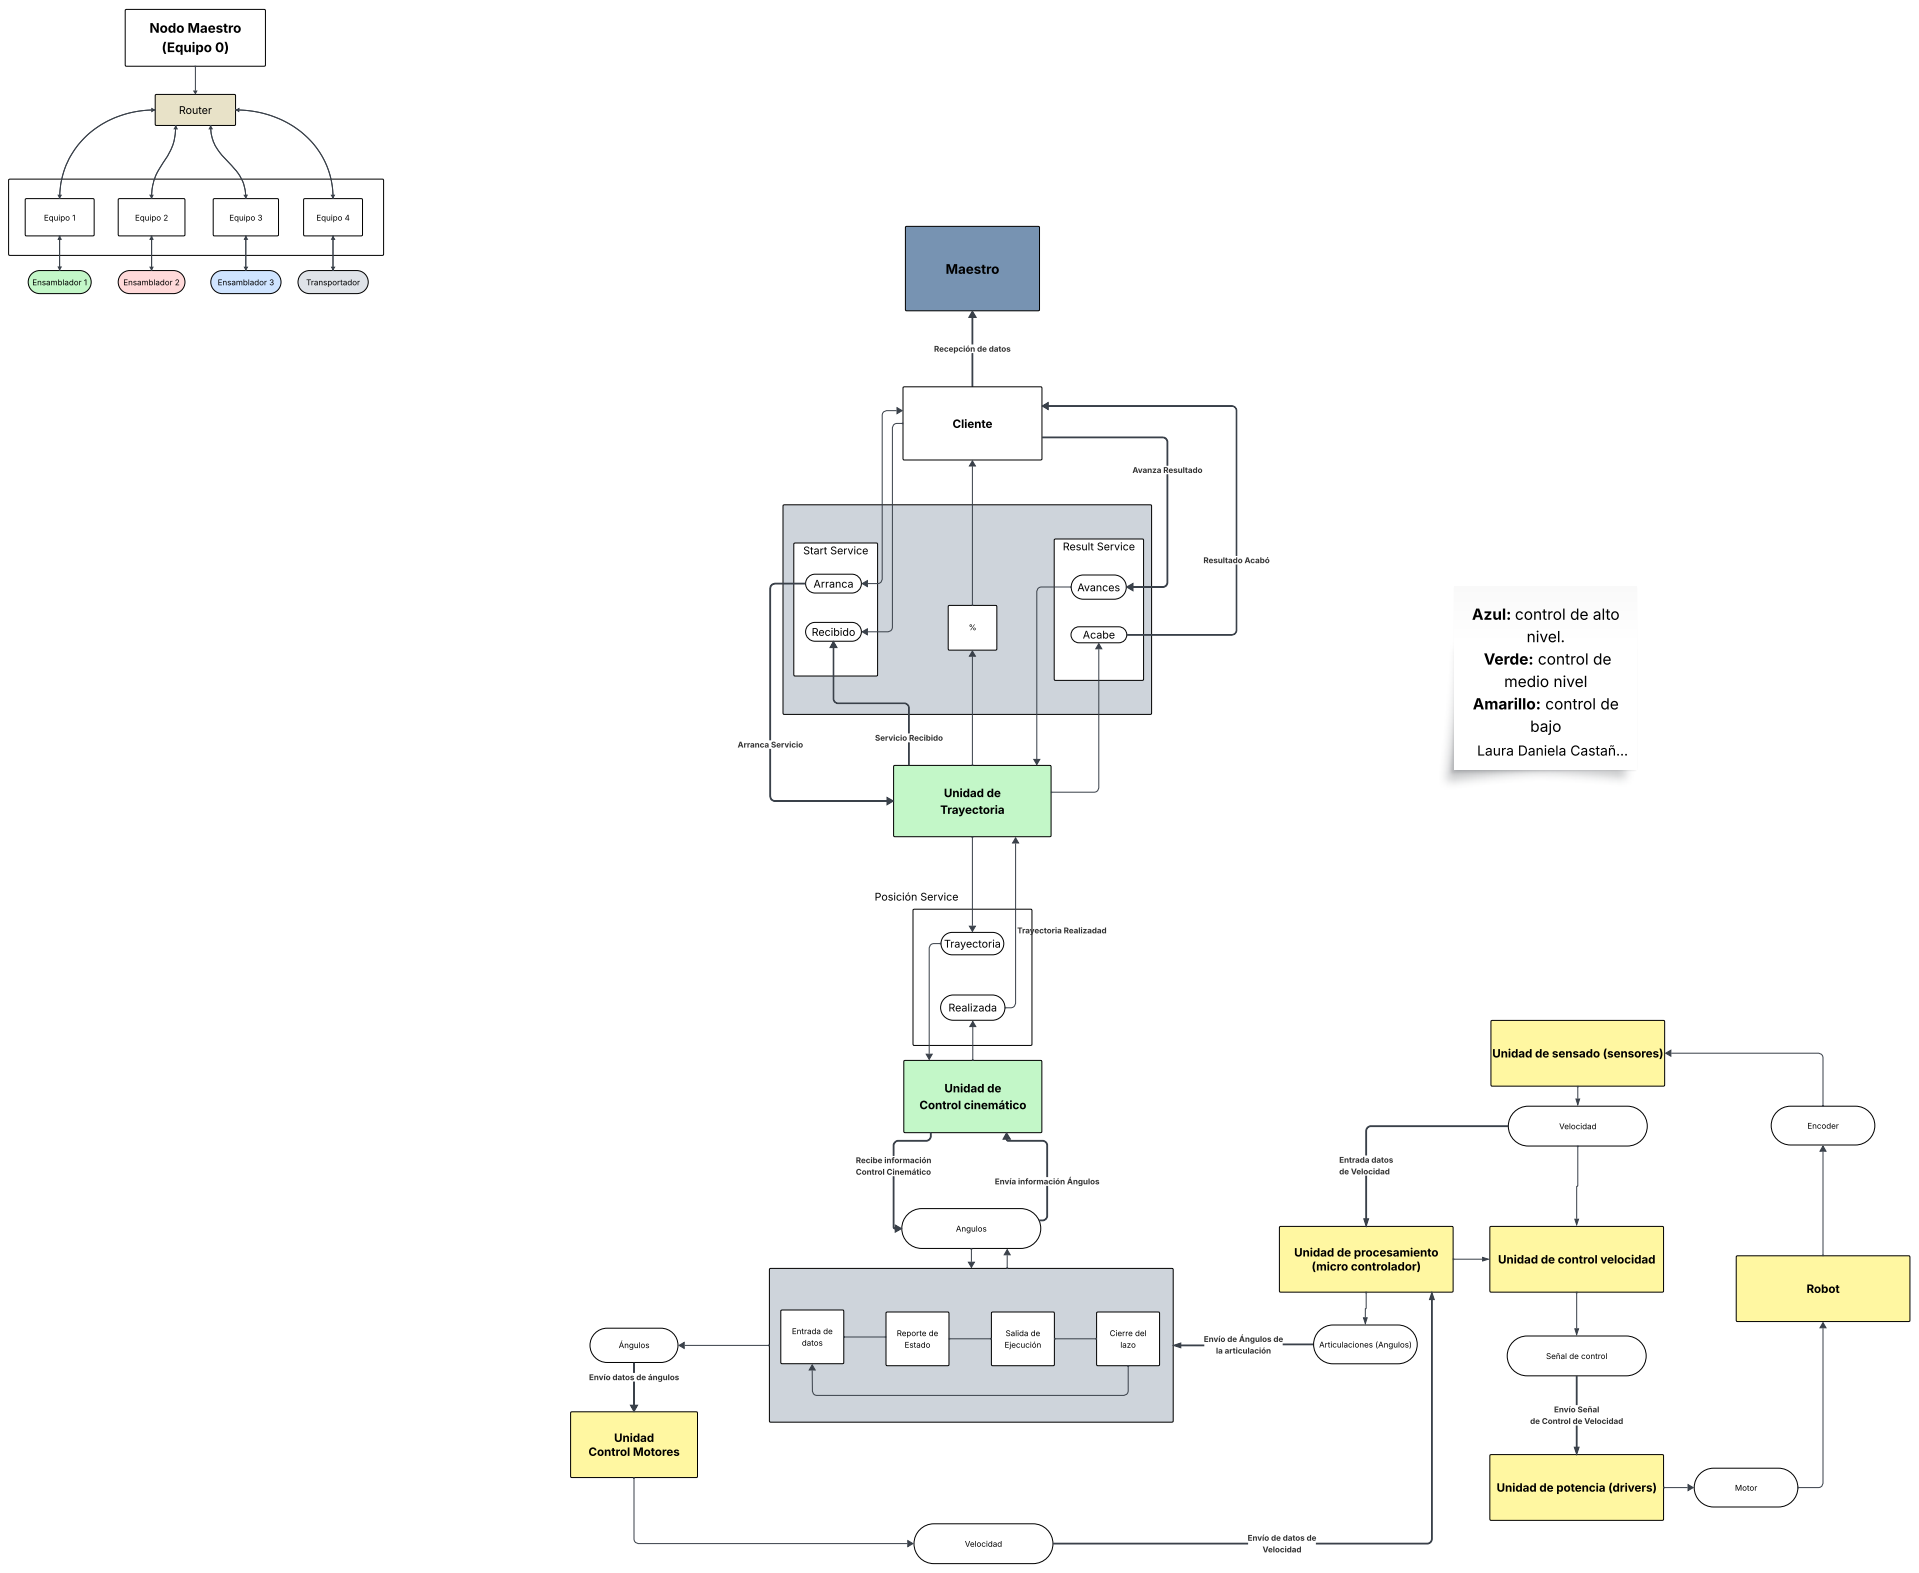
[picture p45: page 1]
Start Service; Arranca; Recibido; Realizada; Trayectoria; Result Service; Avances; Router; Equipo 1; Equipo 2; Equipo 3; Equipo 4; Ensamblador 1; Ensamblador 2; Ensamblador 3; Transportador; Maestro; bajo; Cliente; Acabe; Avanza Resultado; Resultado Acabó; Unidad de Trayectoria; Servicio Recibido; Arranca Servicio; Trayectoria Realizadad; Posición Service; Unidad de Control cinemático; Entrada de datos; Reporte de Estado; Salida de Ejecución; Cierre del lazo; Unidad Control Motores; Ángulos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

Recepción de datos

Azul: control de alto

nivel.
Verde: control de
medio nivel
Amarillo: control de

Laura Daniela Castañ?

Unidad de sensado (sensores)

Envía información Ángulos

Unidad de procesamiento
(micro controlador)

Unidad de control velocidad

Envío de Ángulos de
la articulación

Señal de control

Envío datos de ángulos

Envío Señal
de Control de Velocidad

Unidad de potencia (drivers)

Envío de datos de
Velocidad

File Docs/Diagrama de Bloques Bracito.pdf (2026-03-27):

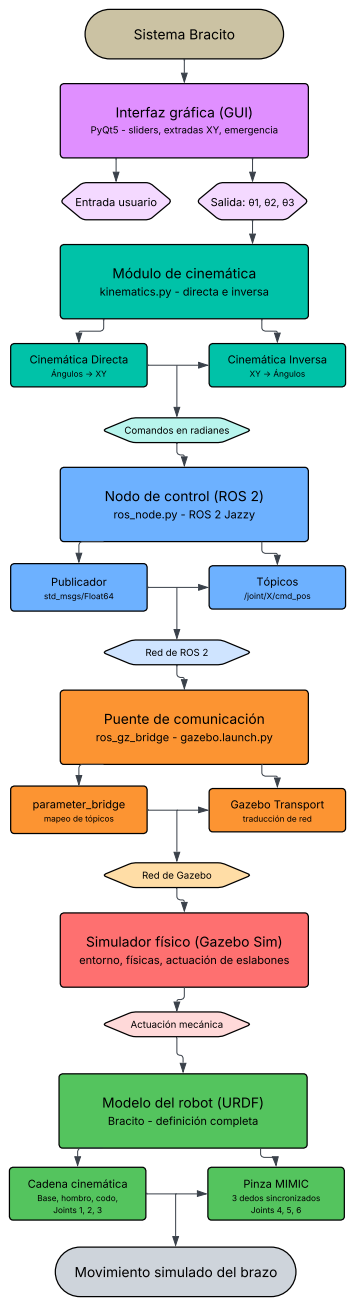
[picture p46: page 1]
Sistema Bracito; Entrada usuario; Salida: ?1, ?2, ?3; Cinemática Directa; Ángulos ? XY; Cinemática Inversa; XY ? Ángulos; Publicador; std_msgs/Float64; Tópicos; /joint/X/cmd_pos; Actuación mecánica; Pinza MIMIC; 3 dedos sincronizados Joints 4, 5, 6

Interfaz gráfica (GUI)
PyQt5 - sliders, extradas XY, emergencia

Módulo de cinemática
kinematics.py - directa e inversa

Comandos en radianes

Nodo de control (ROS 2)
ros_node.py - ROS 2 Jazzy

Red de ROS 2

Puente de comunicación
ros_gz_bridge - gazebo.launch.py

parameter_bridge
mapeo de tópicos

Gazebo Transport
traducción de red

Red de Gazebo

Simulador físico (Gazebo Sim)
entorno, físicas, actuación de eslabones

Modelo del robot (URDF)
Bracito - definición completa

Cadena cinemática
Base, hombro, codo,
Joints 1, 2, 3

Movimiento simulado del brazo

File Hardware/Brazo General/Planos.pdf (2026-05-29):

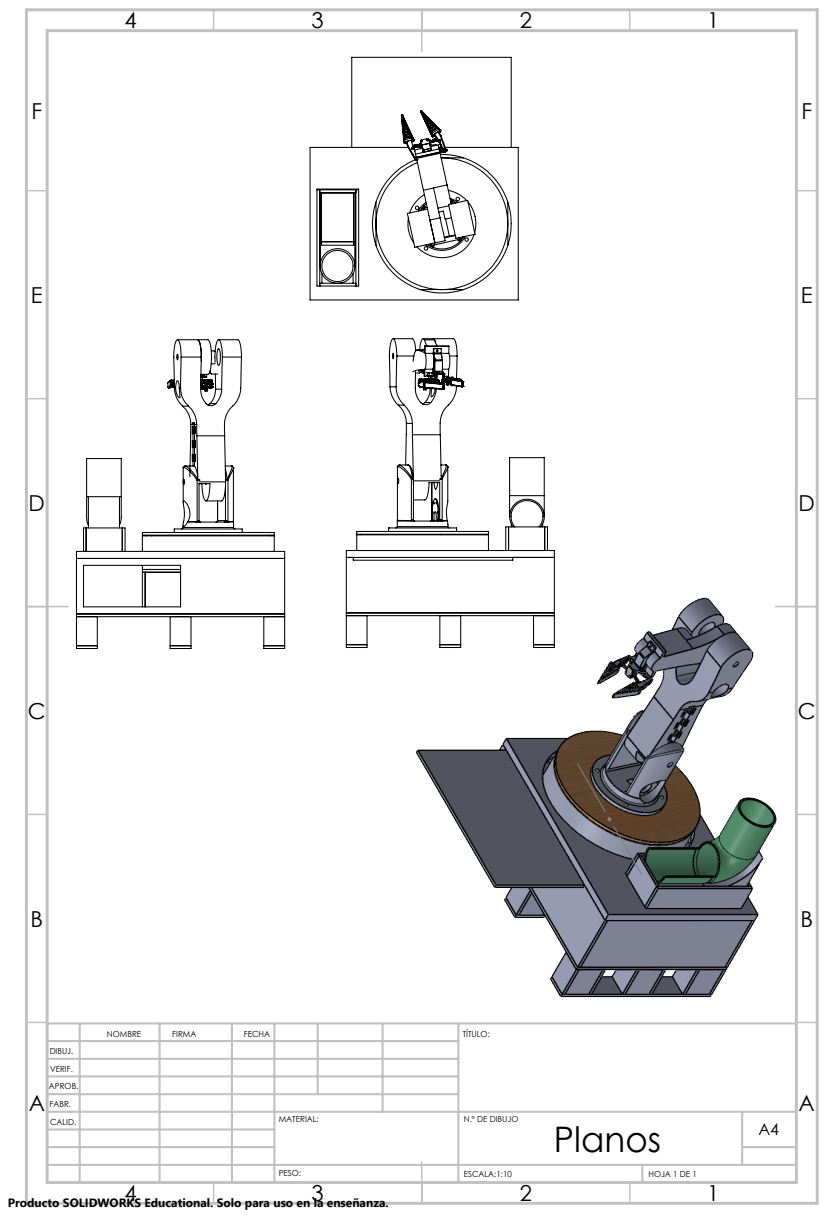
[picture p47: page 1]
ESCALA:1:10; HOJA 1 DE 1

NOMBRE | FIRMA | FECHA | | | | TÍTULO:

DIBUJ.
VERIF.
APROB.
FABR.
CALID. | | | | MATERIAL: | N.º DE DIBUJO Planos | A4

Producto SOLIDWORKS Educational. Solo para uso en la enseñanza.

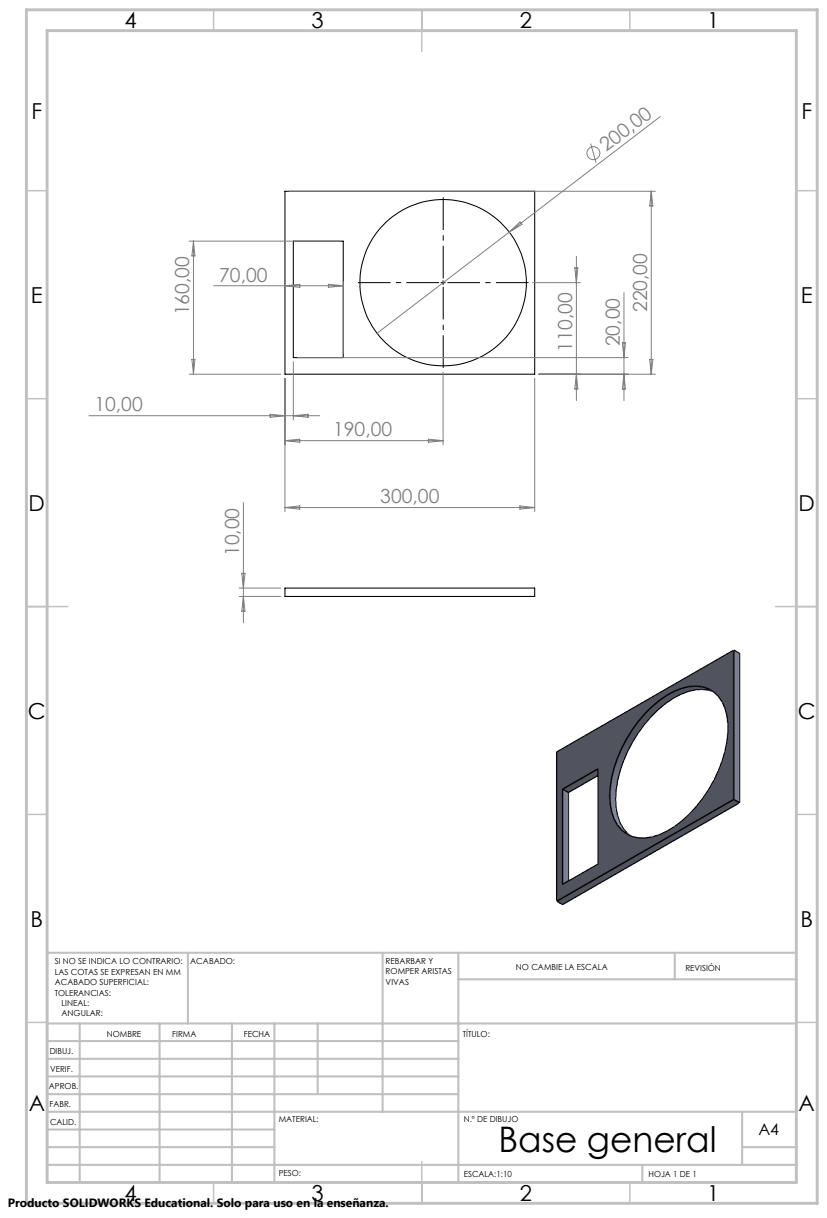
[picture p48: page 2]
ACABADO:; REBARBAR Y; ROMPER ARISTAS; NO CAMBIE LA ESCALA; REVISIÓN

SI NO SE INDICA LO CONTRARIO:
LAS COTAS SE EXPRESAN EN MM
ACABADO SUPERFICIAL:
TOLERANCIAS:
LINEAL:
ANGULAR:

NOMBRE | FIRMA | FECHA | | TÍTULO:

DIBUJ.
VERIF.
APROB.
FABR.

Base general

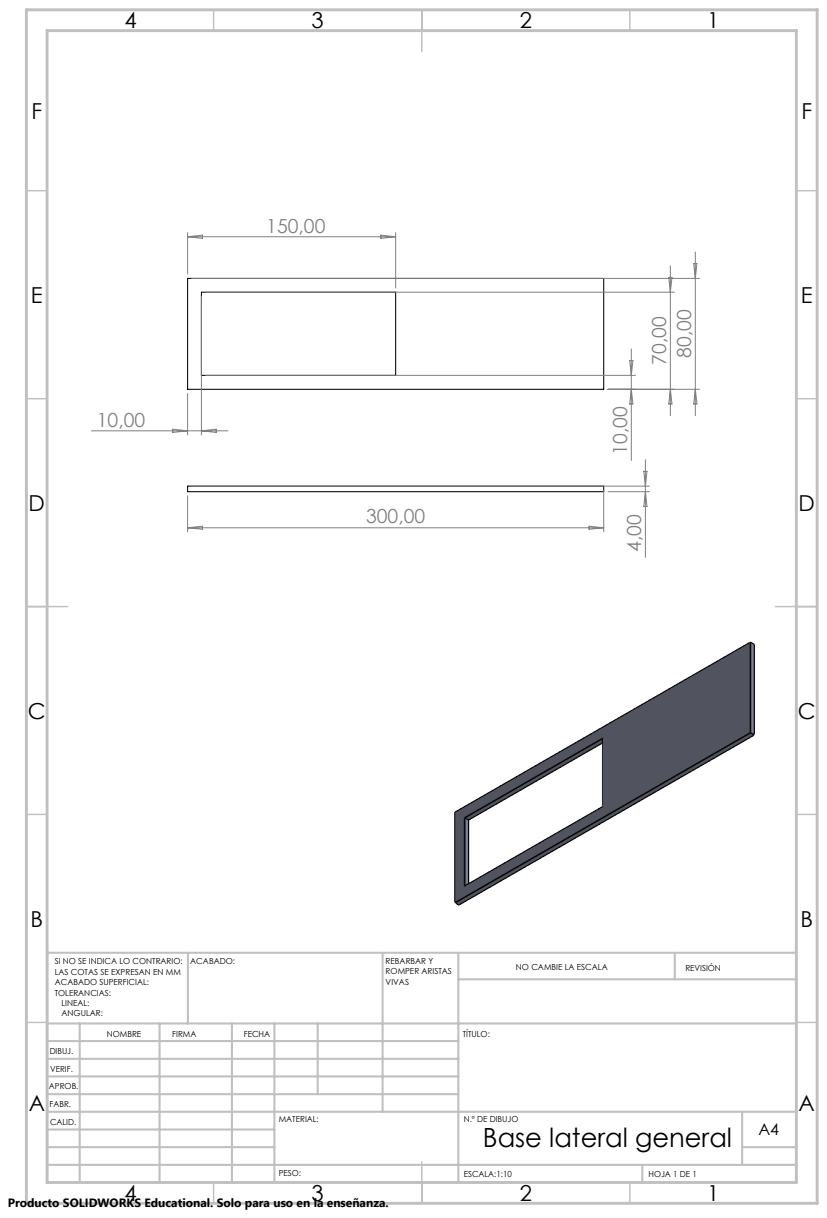
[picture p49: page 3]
ACABADO:; REBARBAR Y; ROMPER ARISTAS; NO CAMBIE LA ESCALA; REVISIÓN

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

NOMBRE | FIRMA | FECHA | | TÍTULO:

DIBUJ.
VERIF.
APROB.
FABR.

Base lateral general

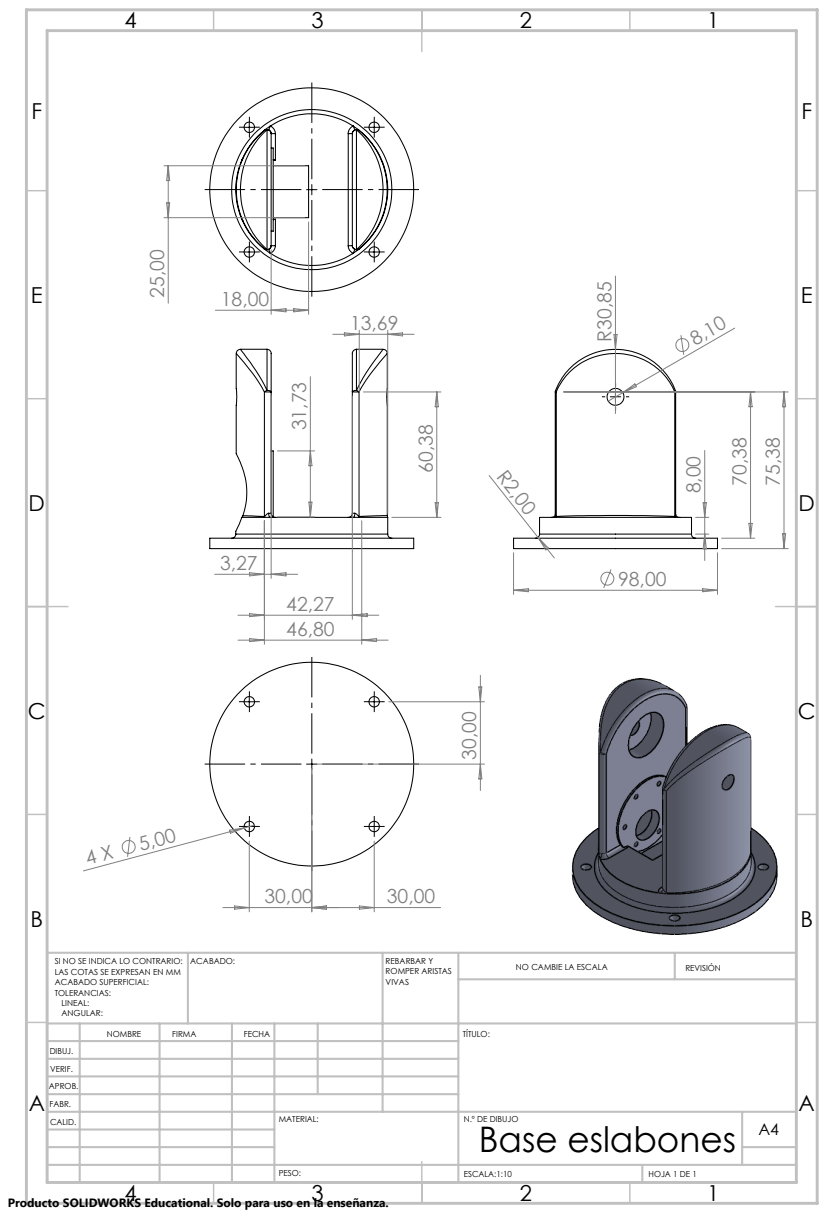
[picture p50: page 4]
ACABADO:; REBARBAR Y; ROMPER ARISTAS; NO CAMBIE LA ESCALA; REVISIÓN

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

NOMBRE | FIRMA | FECHA | | TÍTULO:

DIBUJ.
VERIF.
APROB.
FABR.

Base eslabones

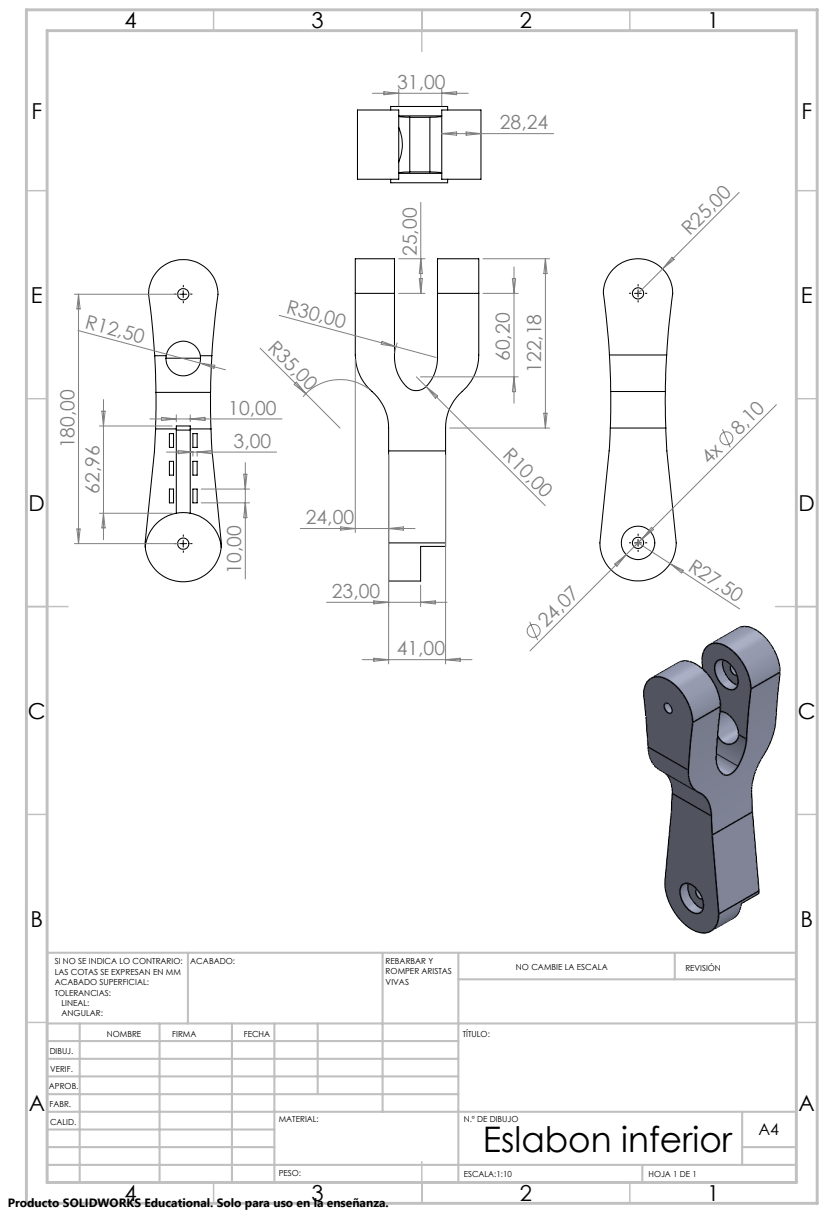
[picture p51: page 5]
ACABADO:; REBARBAR Y; ROMPER ARISTAS; NO CAMBIE LA ESCALA; REVISIÓN

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

NOMBRE | FIRMA | FECHA | | TÍTULO:

DIBUJ.
VERIF.
APROB.
FABR.

Eslabon inferior

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

NOMBRE | FIRMA | FECHA | | TÍTULO:

DIBUJ.
VERIF.
APROB.
FABR.

Eslabon superior

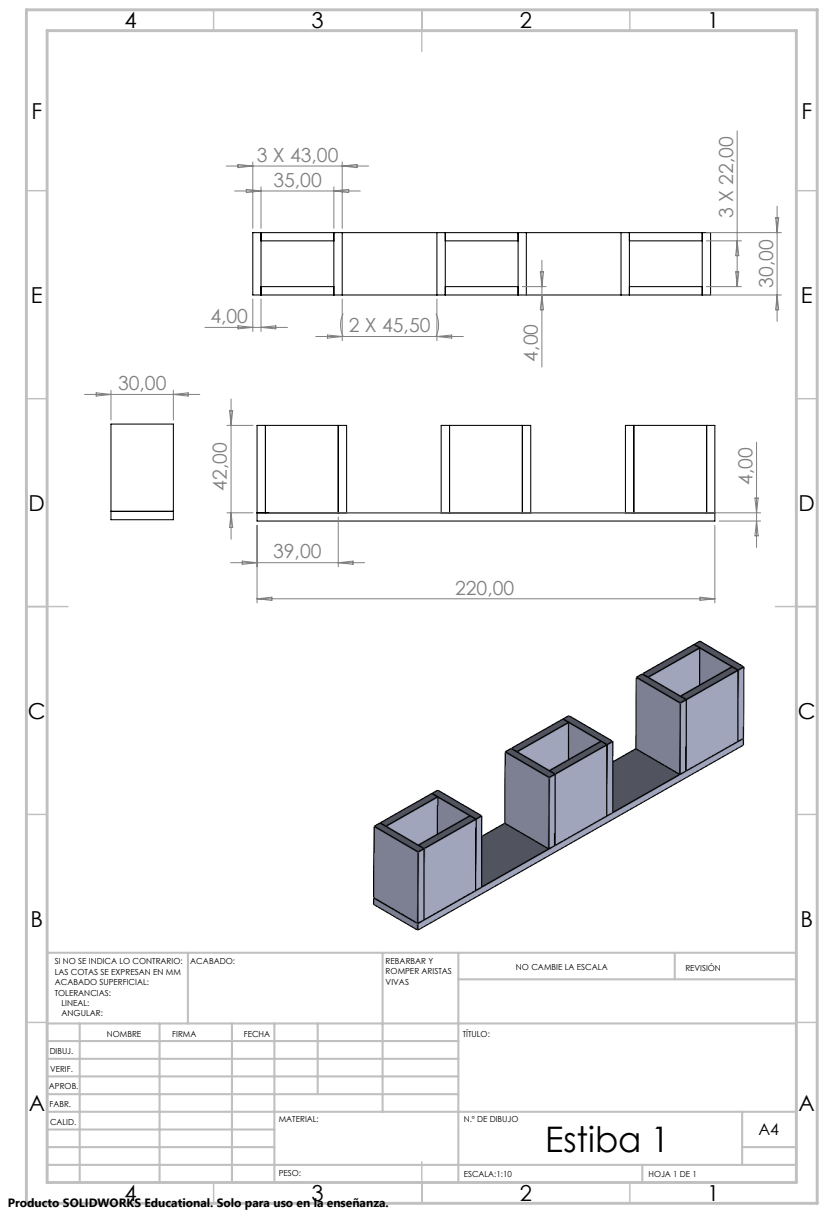
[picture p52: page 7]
ACABADO:; REBARBAR Y; ROMPER ARISTAS; NO CAMBIE LA ESCALA; REVISIÓN

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

NOMBRE | FIRMA | FECHA | | TÍTULO:

DIBUJ.
VERIF.
APROB.
FABR.

Estiba 1

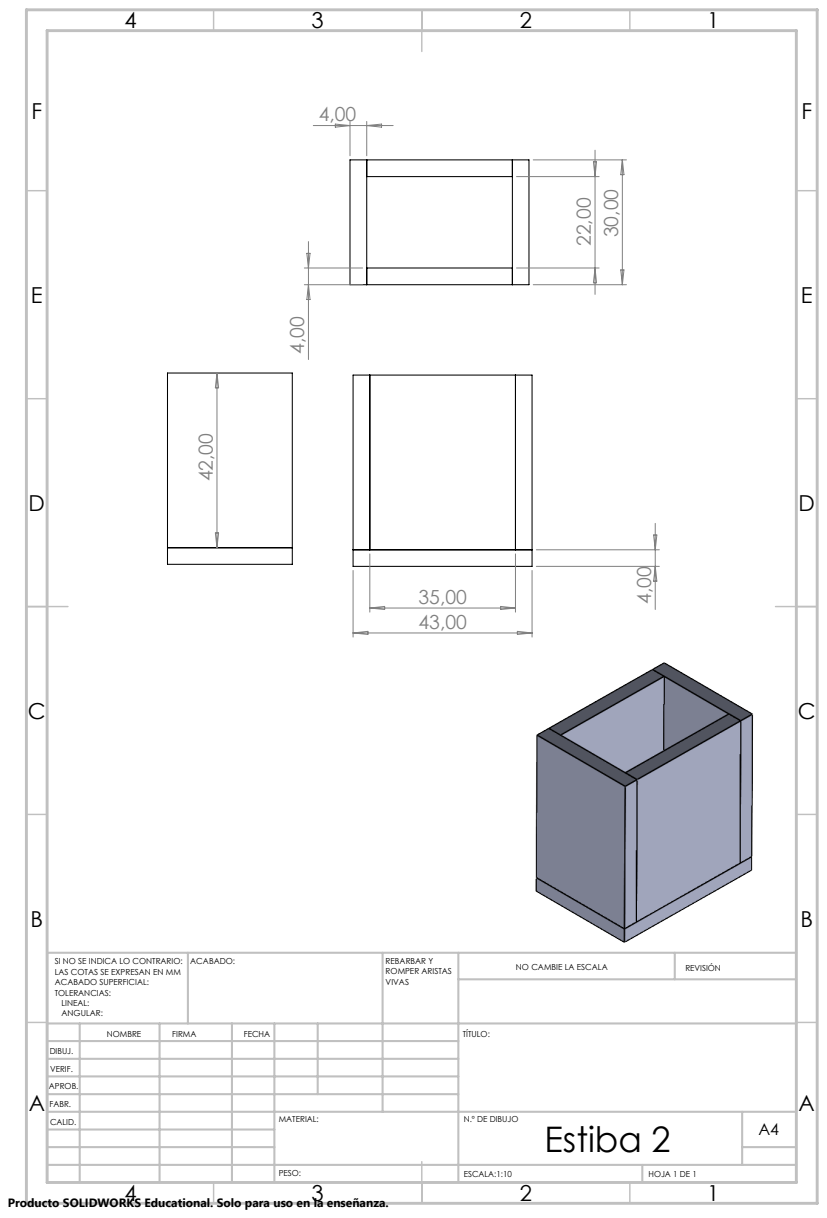
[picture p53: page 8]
ACABADO:; REBARBAR Y; ROMPER ARISTAS; NO CAMBIE LA ESCALA; REVISIÓN

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

NOMBRE | FIRMA | FECHA | | TÍTULO:

DIBUJ.
VERIF.
APROB.
FABR.

Estiba 2

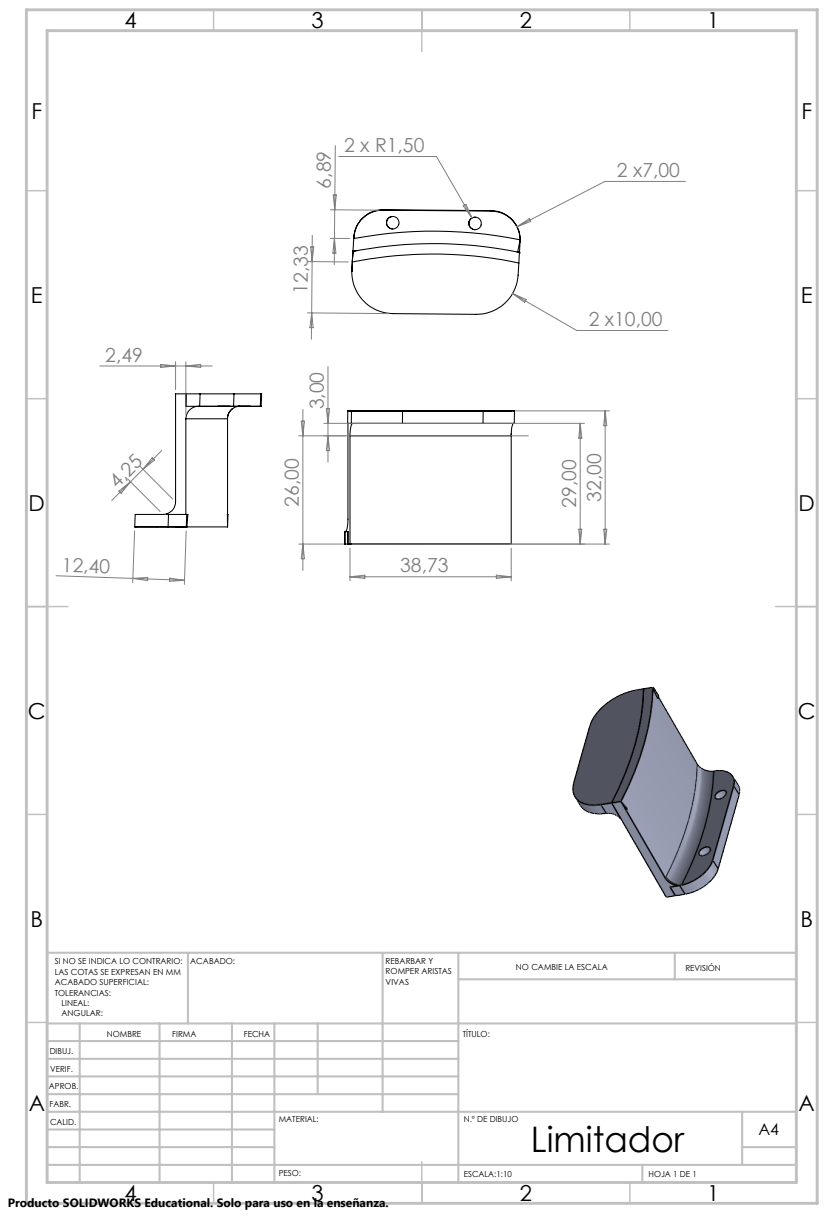
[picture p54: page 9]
ACABADO:; REBARBAR Y; ROMPER ARISTAS; NO CAMBIE LA ESCALA; REVISIÓN

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

NOMBRE | FIRMA | FECHA | | TÍTULO:

DIBUJ.
VERIF.
APROB.
FABR.

Limitador

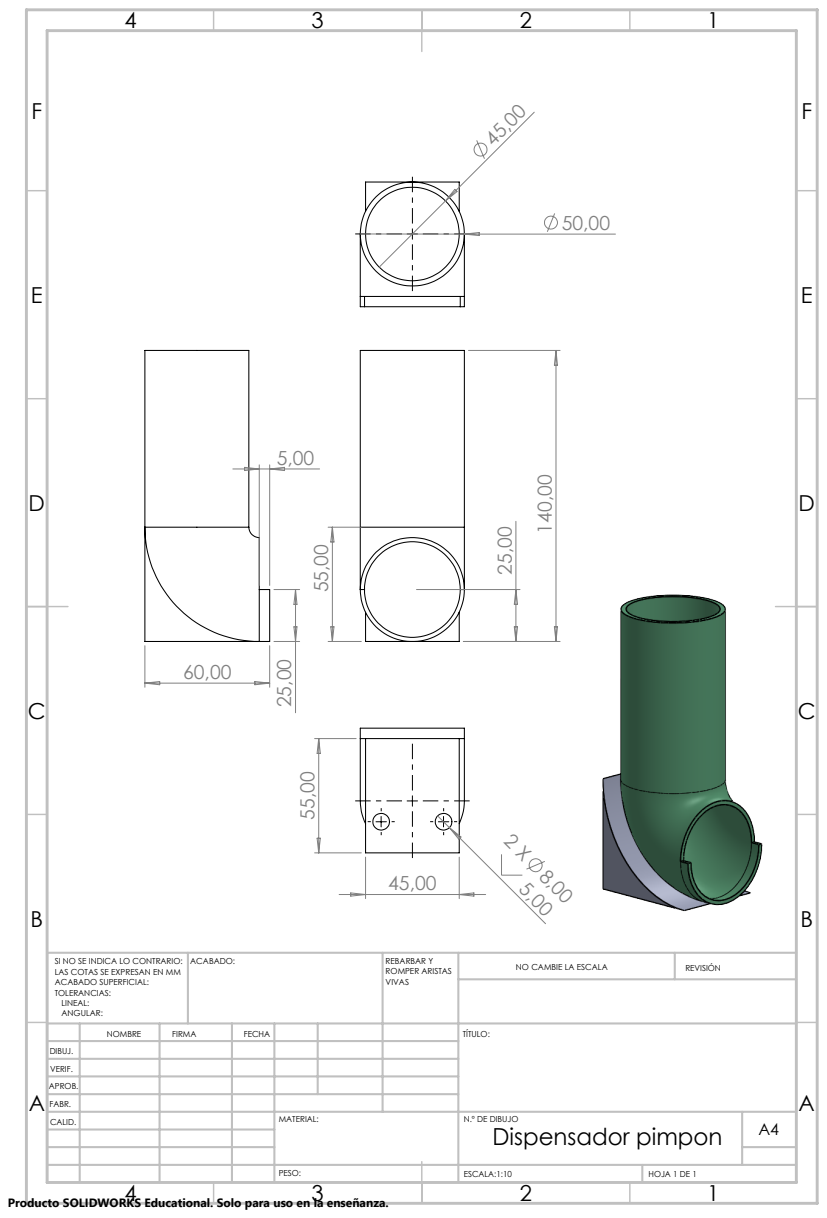
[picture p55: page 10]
ACABADO:; REBARBAR Y; ROMPER ARISTAS; NO CAMBIE LA ESCALA; REVISIÓN

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

NOMBRE | FIRMA | FECHA | | TÍTULO:

DIBUJ.
VERIF.
APROB.
FABR.

Dispensador pimpon

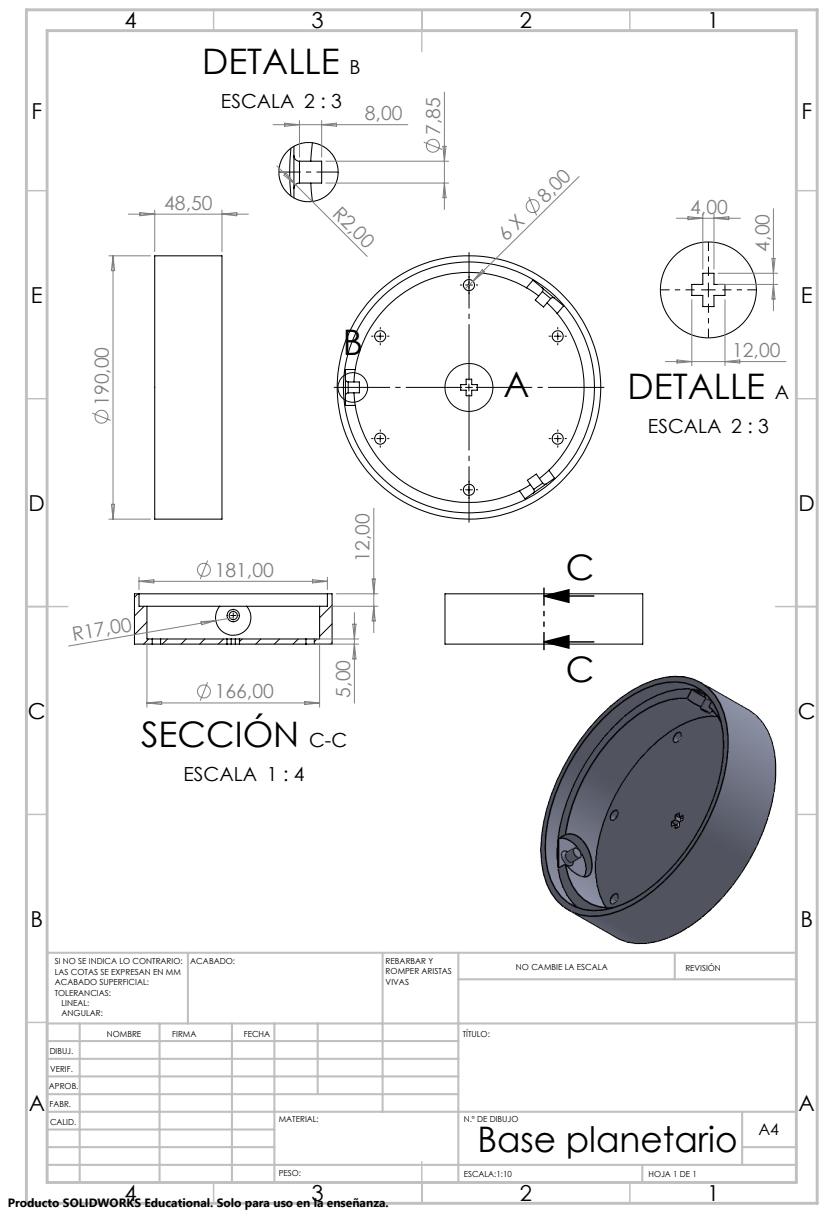
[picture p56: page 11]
DETALLE A; ESCALA 2 : 3; SECCIÓN C-C; ESCALA 1 : 4; DETALLE B; ACABADO:; REBARBAR Y; ROMPER ARISTAS; NO CAMBIE LA ESCALA; REVISIÓN

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

NOMBRE | FIRMA | FECHA | | TÍTULO:

DIBUJ.
VERIF.
APROB.
FABR.

Base planetario

DETALLE E; ESCALA 1 : 1; Módulo 2; ACABADO:; REBARBAR Y; ROMPER ARISTAS; NO CAMBIE LA ESCALA; REVISIÓN

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

NOMBRE | FIRMA | FECHA | | TÍTULO:

DIBUJ.
VERIF.
APROB.
FABR.

Engranaje Planetario

ACABADO:; REBARBAR Y; ROMPER ARISTAS; NO CAMBIE LA ESCALA; REVISIÓN

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

NOMBRE | FIRMA | FECHA | | TÍTULO:

DIBUJ.
VERIF.
APROB.
FABR.

Soporte Planetario

SECCIÓN F-F; ESCALA 1 : 1; ACABADO:; REBARBAR Y; ROMPER ARISTAS; NO CAMBIE LA ESCALA; REVISIÓN

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

NOMBRE | FIRMA | FECHA | | TÍTULO:

DIBUJ.
VERIF.
APROB.
FABR.

Limitador Planetario

ACABADO:; REBARBAR Y; ROMPER ARISTAS; NO CAMBIE LA ESCALA; REVISIÓN

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

NOMBRE | FIRMA | FECHA | | TÍTULO:

DIBUJ.
VERIF.
APROB.
FABR.

Base motor

ACABADO:; REBARBAR Y; ROMPER ARISTAS; NO CAMBIE LA ESCALA; REVISIÓN

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

NOMBRE | FIRMA | FECHA | | TÍTULO:

DIBUJ.
VERIF.
APROB.
FABR.

Ajuste rodamiento
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

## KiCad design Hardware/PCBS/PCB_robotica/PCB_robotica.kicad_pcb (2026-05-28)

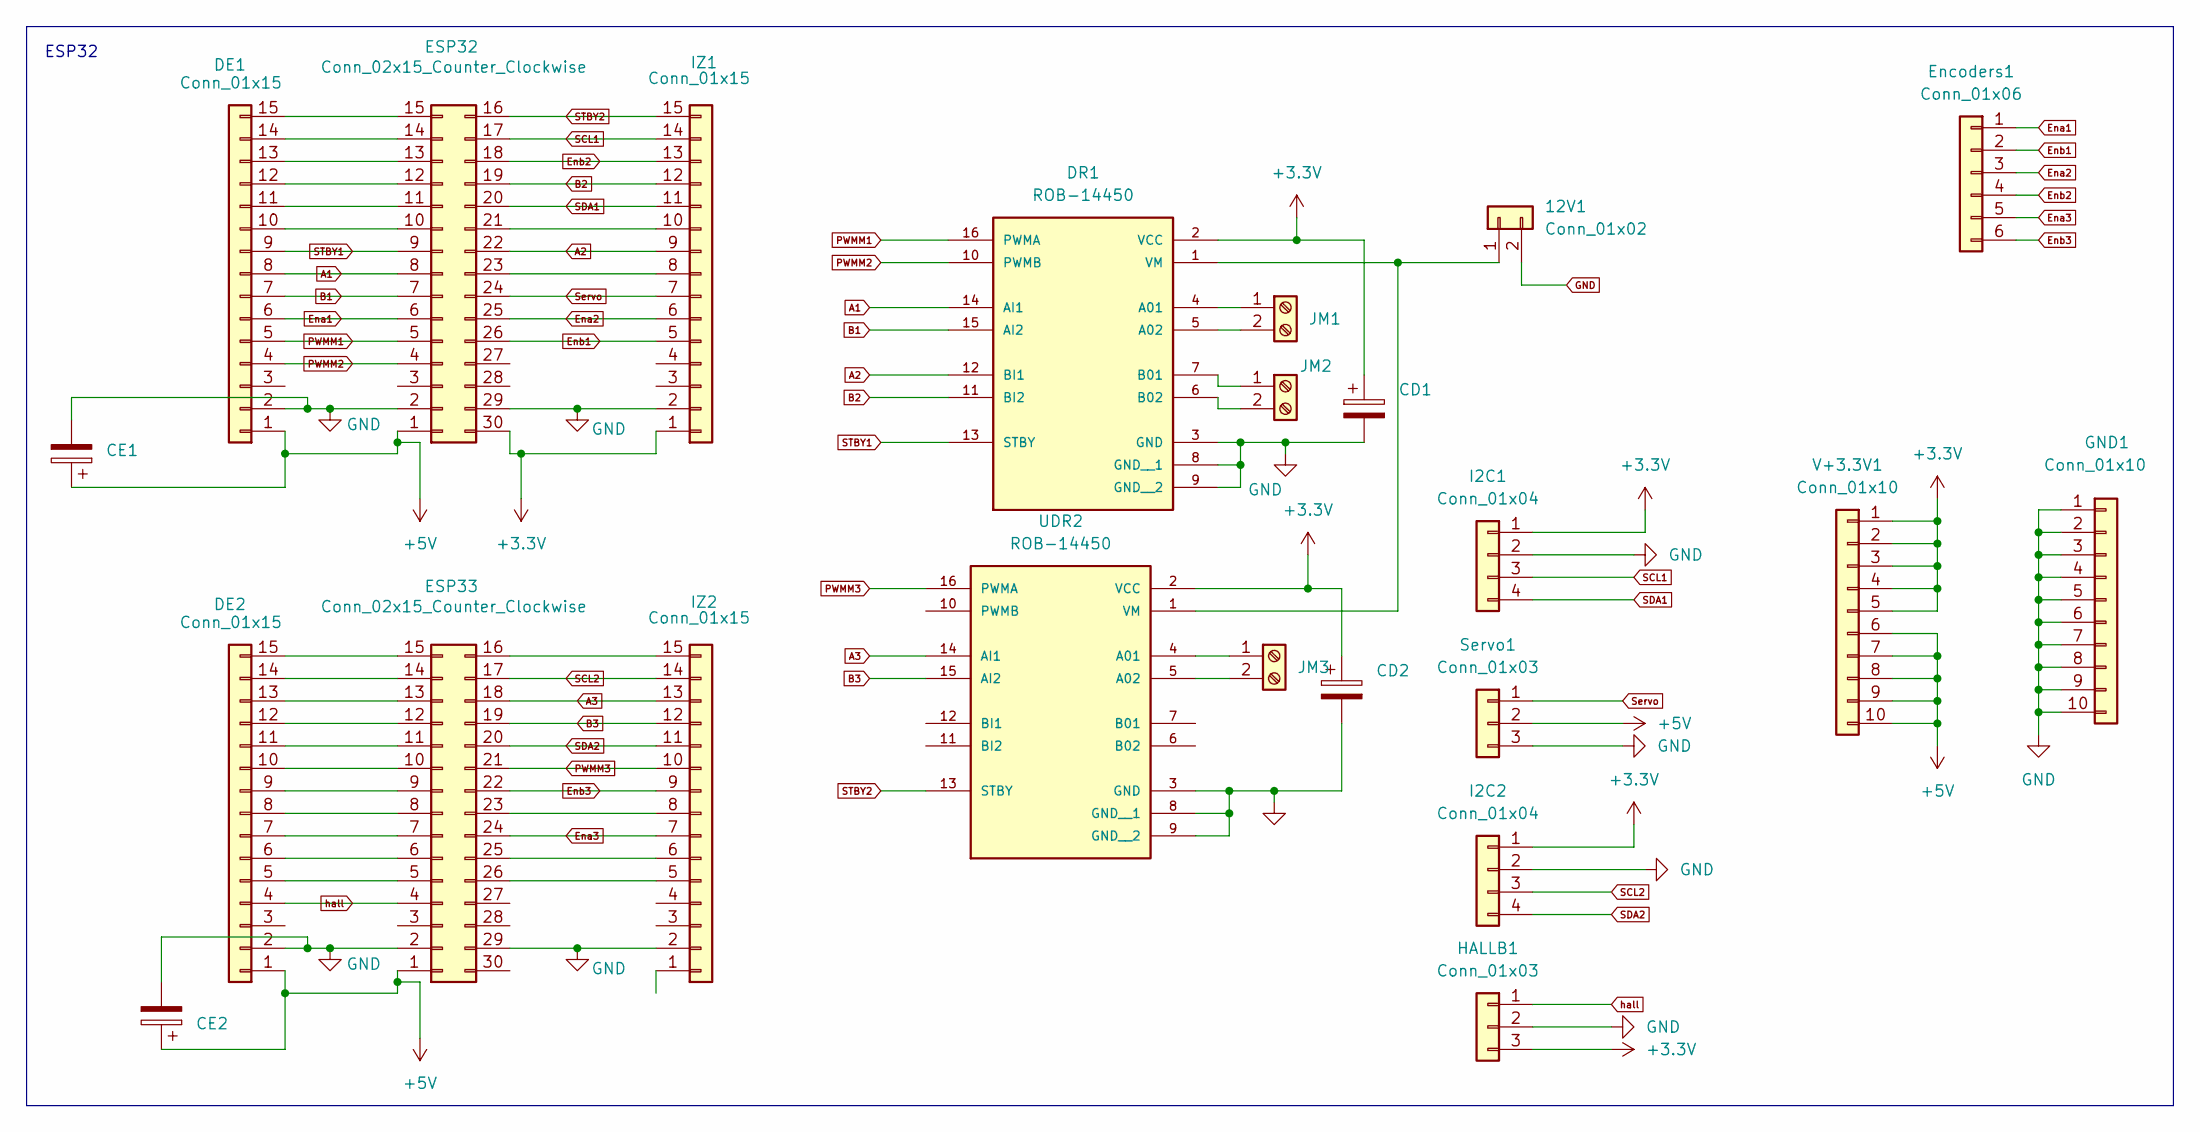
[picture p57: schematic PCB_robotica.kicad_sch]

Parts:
12V1: Conn_01x02; PinHeader_1x02_P2.54mm_Vertical
CD1, CD2: C_Polarized; CP_Radial_Tantal_D10.5mm_P5.00mm
CE1, CE2: C_Polarized; CP_Radial_Tantal_D10.5mm_P5.00mm
DE1, DE2: Conn_01x15; PinHeader_1x15_P2.00mm_Vertical
DR1: ROB-14450; MODULE_ROB-14450; PARTREV 11-13-17
ESP32, ESP33: Conn_02x15_Counter_Clockwise; ESP32-C3-DevKitM-1
Encoders1: Conn_01x06; PinHeader_1x06_P2.54mm_Vertical
GND1: Conn_01x10; PinHeader_1x10_P2.54mm_Vertical
HALLB1: Conn_01x03; PinHeader_1x03_P2.54mm_Vertical
I2C1, I2C2: Conn_01x04; PinHeader_1x04_P2.54mm_Vertical
IZ1, IZ2: Conn_01x15; PinHeader_1x15_P2.54mm_Vertical
JM1, JM2, JM3: Screw_Terminal_01x02; TerminalBlock_MaiXu_MX126-5.0-02P_1x02_P5.00mm
Servo1: Conn_01x03; PinHeader_1x03_P2.54mm_Vertical
UDR2: ROB-14450; MODULE_ROB-14450; PARTREV 11-13-17
V+3.3V1: Conn_01x10; PinSocket_1x10_P2.54mm_Vertical

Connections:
+3.3V: CD1.1, CD2.1, DR1.2 (VCC), ESP32.30, HALLB1.3, I2C1.1, I2C2.1, IZ1.1, UDR2.2 (VCC), V+3.3V1.1, V+3.3V1.2, V+3.3V1.3, V+3.3V1.4, V+3.3V1.5
+5V: CE1.1, CE2.1, DE1.1, DE2.1, ESP32.1, ESP33.1, Servo1.2, V+3.3V1.6, V+3.3V1.7, V+3.3V1.8, V+3.3V1.9, V+3.3V1.10
A1: DE1.8, DR1.14 (AI1), ESP32.8
A2: DR1.12 (BI1), ESP32.22, IZ1.9
A3: ESP33.18, IZ2.13, UDR2.14 (AI1)
B1: DE1.7, DR1.15 (AI2), ESP32.7
B2: DR1.11 (BI2), ESP32.19, IZ1.12
B3: ESP33.19, IZ2.12, UDR2.15 (AI2)
Ena1: DE1.6, ESP32.6, Encoders1.1
Ena2: ESP32.25, Encoders1.3, IZ1.6
Ena3: ESP33.24, Encoders1.5, IZ2.7
Enb1: ESP32.26, Encoders1.2, IZ1.5
Enb2: ESP32.18, Encoders1.4, IZ1.13
Enb3: ESP33.22, Encoders1.6, IZ2.9
GND: 12V1.2, CD1.2, CD2.2, CE1.2, CE2.2, DE1.2, DE2.2, DR1.3 (GND), DR1.8 (GND__1), DR1.9 (GND__2), ESP32.2, ESP32.29, ESP33.2, ESP33.29, GND1.1, GND1.2, GND1.3, GND1.4, GND1.5, GND1.6, GND1.7, GND1.8, GND1.9, GND1.10, HALLB1.2, I2C1.2, I2C2.2, IZ1.2, IZ2.2, Servo1.3, UDR2.3 (GND), UDR2.8 (GND__1), UDR2.9 (GND__2)
unnamed: 12V1.1, DR1.1 (VM), UDR2.1 (VM)
unnamed: DE1.10, ESP32.10
unnamed: DE1.11, ESP32.11
unnamed: DE1.12, ESP32.12
unnamed: DE1.13, ESP32.13
unnamed: DE1.14, ESP32.14
unnamed: DE1.15, ESP32.15
unnamed: DE2.5, ESP33.5
unnamed: DE2.6, ESP33.6
unnamed: DE2.7, ESP33.7
unnamed: DE2.8, ESP33.8
unnamed: DE2.9, ESP33.9
unnamed: DE2.10, ESP33.10
unnamed: DE2.11, ESP33.11
unnamed: DE2.12, ESP33.12
unnamed: DE2.13, ESP33.13
unnamed: DE2.14, ESP33.14
unnamed: DE2.15, ESP33.15
unnamed: DR1.4 (A01), JM1.1
unnamed: DR1.5 (A02), JM1.2
unnamed: DR1.7 (B01), JM2.1
unnamed: DR1.6 (B02), JM2.2
unnamed: ESP32.21, IZ1.10
unnamed: ESP32.23, IZ1.8
unnamed: ESP33.16, IZ2.15
unnamed: ESP33.23, IZ2.8
unnamed: ESP33.25, IZ2.6
unnamed: ESP33.26, IZ2.5
unnamed: JM3.1, UDR2.4 (A01)
unnamed: JM3.2, UDR2.5 (A02)
PWMM1: DE1.5, DR1.16 (PWMA), ESP32.5
PWMM2: DE1.4, DR1.10 (PWMB), ESP32.4
PWMM3: ESP33.21, IZ2.10, UDR2.16 (PWMA)
SCL1: ESP32.17, I2C1.3, IZ1.14
SCL2: ESP33.17, I2C2.3, IZ2.14
SDA1: ESP32.20, I2C1.4, IZ1.11
SDA2: ESP33.20, I2C2.4, IZ2.11
STBY1: DE1.9, DR1.13 (STBY), ESP32.9
STBY2: ESP32.16, IZ1.15, UDR2.13 (STBY)
Servo: ESP32.24, IZ1.7, Servo1.1
hall: DE2.4, ESP33.4, HALLB1.1

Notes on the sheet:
ESP32

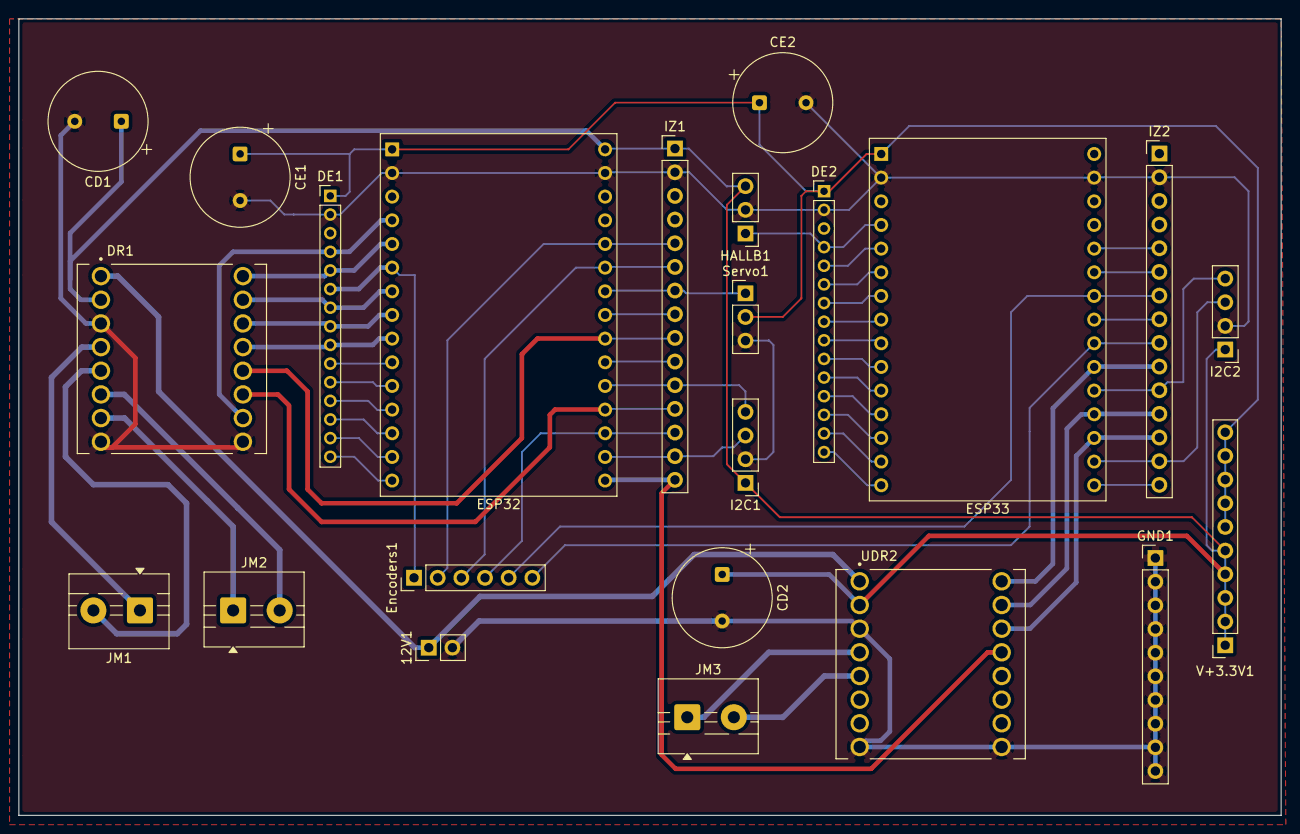
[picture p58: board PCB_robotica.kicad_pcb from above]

Board: 2 copper layers, 135.5 x 85.5 mm, 23 parts (0 on the bottom side), 56 nets.

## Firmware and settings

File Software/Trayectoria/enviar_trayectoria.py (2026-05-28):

import serial
import time
import math
import os

# === 1. CONFIGURACIÓN IMPORTANTE ===
PUERTO = 'COM3' 
BAUDIOS = 115200
NOMBRE_ARCHIVO = 'Brazolauracarol.txt' 

# === EL TRUCO DE MAGIA PARA LAS CARPETAS ===
# Esto obliga a Python a buscar en la misma carpeta del script, pase lo que pase.
directorio_script = os.path.dirname(os.path.abspath(__file__))
ruta_completa = os.path.join(directorio_script, NOMBRE_ARCHIVO)

try:
    print(f"1. Intentando conectar al ESP32 en el puerto {PUERTO}...")
    esp32 = serial.Serial(PUERTO, BAUDIOS)
    time.sleep(2) 
    print("2. ¡ESP32 Conectado exitosamente!")
    
    print(f"3. Abriendo el archivo exactamente en:\n   {ruta_completa}")
    with open(ruta_completa, 'r') as file:
        next(file) # Saltar la primera línea (t,q1,q2,q3)
        
        print("4. ¡Atención! Iniciando movimiento en 3 segundos...")
        time.sleep(3)
        
        for linea in file:
            valores = linea.strip().split(',')
            if len(valores) == 4:
                t = float(valores[0])
                q1_rad = float(valores[1])
                
                # Convertimos tu radian a grados
                q1_deg = q1_rad * (180.0 / math.pi)
                
                # Le enviamos el grado al ESP32
                esp32.write(f"{q1_deg}\n".encode())
                print(f"Tiempo: {t}s -> Enviando M1: {q1_deg:.2f}°")
                
                # Respetamos el salto de tu simulador (0.05 segundos)
                time.sleep(0.05)
                
    print("\n¡Trayectoria terminada con éxito!")
    esp32.close()

except FileNotFoundError:
    print(f"\n[ERROR] Sigo sin encontrar el archivo.")
    print("¿Posible solución? Revisa que Windows no lo haya guardado como 'Brazolauracarol.txt.txt'.")
    print("Intenta renombrar el archivo en tu carpeta a solo 'Brazolauracarol' (sin el .txt al final).")
except serial.SerialException:
    print(f"\n[ERROR] El puerto {PUERTO} está bloqueado o no existe.")
except Exception as e:
    print(f"\n[ERROR DESCONOCIDO]: {e}")

input("\nPresiona ENTER para salir...")

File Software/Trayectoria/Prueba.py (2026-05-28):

import serial
import time
import math

# 1. Configura el puerto donde está tu ESP32 (Ej: 'COM3' en Windows o '/dev/ttyUSB0' en Mac/Linux)
PUERTO = 'COM3' 
BAUDIOS = 115200

try:
    print(f"Conectando al ESP32 en {PUERTO}...")
    esp32 = serial.Serial(PUERTO, BAUDIOS)
    time.sleep(2) # Esperar a que el ESP32 reinicie la conexión
    print("Conectado. Iniciando streaming de trayectoria...")
    
    with open('Brazolauracarol.txt', 'r') as file:
        next(file) # Saltamos la primera línea (el encabezado t,q1,q2,q3)
        
        for linea in file:
            valores = linea.strip().split(',')
            if len(valores) == 4:
                t = float(valores[0])
                q1_rad = float(valores[1])
                
                # Convertir radianes a grados
                q1_deg = q1_rad * (180.0 / math.pi)
                
                # Enviar el ángulo al ESP32 terminado en un salto de línea
                esp32.write(f"{q1_deg}\n".encode())
                
                print(f"Tiempo: {t}s -> Enviado M1: {q1_deg:.2f}°")
                
                # El archivo tiene incrementos de 0.05s (50ms). Respetamos esa velocidad.
                time.sleep(0.05)
                
    print("¡Trayectoria de Gazebo enviada con éxito!")
    esp32.close()

except Exception as e:
    print(f"Error de conexión o lectura: {e}")

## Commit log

2026-03-27 Primer commit: Estructura base, CAD, simulador y GUI
    [Base Rotatorio.SLDPRT, Base alta delantera con hueco.SLDPRT, Base alta delantera.SLDPRT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]
2026-04-10 Actualización de códigos MATLAB, software y simulación
    [Ensamblee.csv, Ensamblee.urdf, base_giratoria.STL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]
2026-05-28 Agregando carpetas de hardware, pinza y simulaciones
    [Grupocarlitos.DXF, Grupocarlitos.SLDPRT, Laurayyo.DXF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]
2026-05-29 Agregando carpetas de hardware y planos
